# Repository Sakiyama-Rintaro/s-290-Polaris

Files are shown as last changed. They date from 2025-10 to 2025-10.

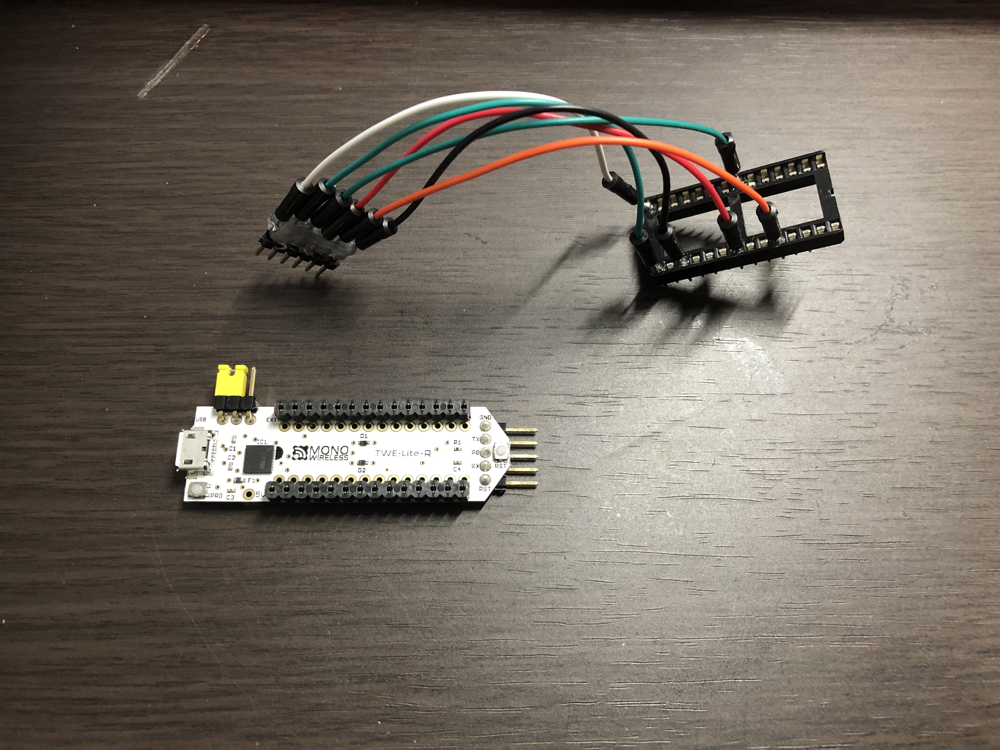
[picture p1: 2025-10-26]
doc/sozai/twelite_programmer.jpg

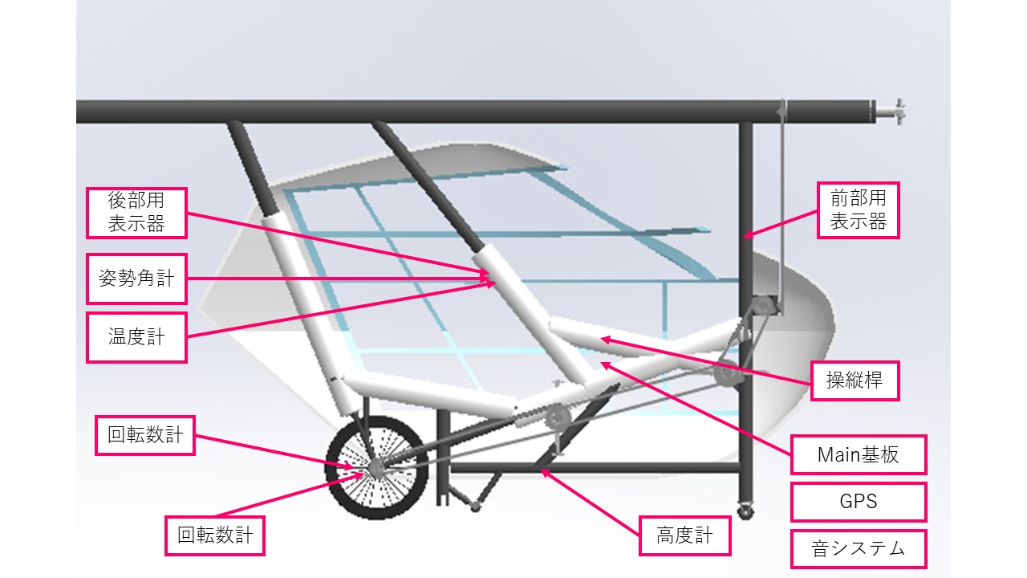
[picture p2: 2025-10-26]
doc/sozai/S-270_Malus_Setsugo_2.jpg

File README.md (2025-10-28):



# S-290 Polaris 電装システム

## はじめに
初めまして。芝浦工業大学理工学研究科電気電子情報学専攻M1の先山倫太郎です。学部時代の学科は工学部電子工学科です。私は学部時代に鳥人間部に所属していて人力飛行機の製作を行っていました。そこでは電装班と呼ばれる機体のシステム系の開発を行なっている班に所属していて、機体の操舵システムと、高度計などの計測器のシステム開発を行っていました。その詳細についてここでは述べさせていただきます。元々プログラミングに興味があり、何かヒントが得られるのではと思い電装班に入った次第です。<br>
<br>
<br>
このリポジトリでは、**人力飛行機電装システム**において<br>
・Mainプリント基板設計・製作<br>
・計測システム・ソフトウェア設計・製作<br>
・操舵システム・ソフトウェア設計・製作<br>
・各種試験系(回転試験・ER試験・全体接合・TF)<br>
に関することが詰まっています。<br>
<br>

なお、フライトデータ表示用のアプリ開発については次のリポジトリを参考にしてください。Androidアプリ開発、Webアプリ開発やその運用方法について記述してあります。<br>
https://github.com/Sakiyama-Rintaro/FlightDisplay.S290<br>

## 後輩の皆さんへ
我々23代電装班では、「同期や後輩の為にしっかりと技術資料を残す」という方針で活動していました。それは、教え合いの文化を形成し効率的な技術力アップを図るためであったり、悲願の鳥コン出場を達成した代なのでこの文化はぜひ引き継いでいったほしいなと思っています。僕からの願いです。<br>
モノづくりを楽しんで、充実した大学生活を送ってください！！<br>

## リポジトリの説明
**・[TBT_S-290_Polaris_System](https://github.com/Sakiyama-Rintaro/s-290-Polaris/tree/main/Module)** //完成品が入っています。プログラム書き込み方法と基板の取り扱いについては、このリポジトリのREADMEを参考にしてください。<br>
**・[Module](https://github.com/Sakiyama-Rintaro/s-290-Polaris/tree/main/Module)** //単体テストで用いたものが入っています。<br>
**・[Yosan](https://github.com/Sakiyama-Rintaro/s-290-Polaris/tree/main/Yosan)** //S-290での購入品についてのデータが入っています。<br>
**・[doc](https://github.com/Sakiyama-Rintaro/s-290-Polaris/tree/main/doc)** //作ったシステムの写真や動画などが入っています。<br>

## 目次
・はじめに<br>
・ソフトウェア・ハードウェア設計ガイド<br>

## 使ったソフト
・GitHub Desktop (GitHub操作用)<br>
・Visual Studio Code (テキストエディタ mbedのコードを書くときに使います)<br>
・LPCISP.exe (lpc1114にプログラムを書きこむときに使います。後で詳細を説明します)<br>
・Tera Term (ターミナル。シリアル通信のデバッグ、Twelite_シリアル通信アプリのモード変更、ER試験等の時に使います<br>
・Realterm (ターミナル。2進数や16進数のデータの確認に使います。Twelite_シリアル通信アプリ_バイナリモード)<br>
・Google Earth Pro (GPSデータのチェックに使います)<br>
・Android Studio (Androidアプリ開発に使います)<br>
・Autodesk Fusion360 (3DCAD。機速計をはじめとする筐体設計に使用します)<br>
・Autodesk Inventor (3DCAD。機速計をはじめとする筐体設計に使用します)<br>
・AutoCAD Mechanical (2DCAD。3DCADだと寸法が確認しづらいので、確認用にこっちも使います。検図チェックお願いします( ﾟДﾟ))<br>
・EAGLE (回路設計CAD。Main基板の設計に使用します。後で詳細を説明します)<br>

## 使用言語
・C/C++ (mbedで使った)<br>
・Kotlin (Androidアプリ開発で使った)<br>

## 使用マイコン(※主要部のみ)
・mbed LPC1768<br>
・mbed LPC1114<br>

# システム全体図
S-290 Malus電装システムの全体図を示します。<br>
各矢印については、<br>
・黒色: シリアル通信(有線) <br>
・緑色: デジタル通信(有線) <br>
・黄色: Zigbee通信(有線) <br>
・赤色: Bluetooth通信(無線) <br>
・青色: モバイルデータ通信(無線) <br>
となっています。<br>
矢印の方向にデータが飛んでいます。<br>
### システム全体図_その1
S-270_Malus_Sysyem_1

### システム全体図_その2
S-270_Malus_System_2

## 各計器・部品等の役割
|計器・部品名|役割|
|---|---|
|[機速計](https://github.com/Sakiyama-Rintaro/s-290-Polaris/blob/main/Module/Airspeed_meter/README.md)|機体の速度(空気に対する相対速度)を計測する|
|[回転数計](https://github.com/Sakiyama-Rintaro/s-290-Polaris/blob/main/doc/picture/Cadence_meter.md)|パイロット達がペダルを回す速さを計測する|
|[高度計](https://github.com/Sakiyama-Rintaro/s-290-Polaris/blob/main/doc/picture/Altimeter.md)|機体の高度を計測する|
|姿勢角計|機体の姿勢情報を計測する|
|心拍計|フライト時におけるパイロット達の心拍数を計測する|
|温度計|サーボモータ付近の温度を計測する|
|[GPS](https://github.com/Sakiyama-Rintaro/s-290-Polaris/blob/main/doc/picture/GPS.md)|機体の現在位置を計測する|
|SD|機速・回転数・高度・姿勢・心拍数・温度・GPS・舵角等の情報を記録する|
|音システム|機体の高度情報を音で知らせる|
|[舵角計](https://github.com/Sakiyama-Rintaro/s-290-Polaris?tab=readme-ov-file)|ER(サーボモータ)の制御角度を表示する|
|[Android端末](https://github.com/Sakiyama-Rintaro/s-290-Polaris/blob/main/doc/picture/Android.md)|前部パイロットにフライト情報を表示する|
|[OLED](https://github.com/Sakiyama-Rintaro/s-290-Polaris0/blob/main/doc/picture/OLED.md)|後部パイロットにフライト情報を表示する|
|Li-Poバッテリー電圧監視システム|サーボモータ用Li-Poバッテリーの残り電圧の情報を記録する|

## システムの設計方針
S-290のシステムでは、無線モジュールtweliteを多用し計測系統の多機能化とパイロット安全の充実化を目指しました。<br>

## S-250からの変更点
・姿勢角計の導入<br>
・心拍計(前部P・後部P)の導入<br>
・温度計の導入<br>
・Li-poバッテリー電源監視システムの導入<br>
・フライト監視システムの導入<br>
・自作出力計の廃止と市販出力計Germin Vector3の導入<br>
・Mainプリント基板の実装部品の変更<br>
・操舵方式の変更<br>
となっています。

## 本システムの良かった点
・無線モジュールを使って、計測システムの多機能化が出来た点<br>
・無線モジュールを使って、接合時間の短縮を目指せた点<br>
・Li-Poバッテリー電圧監視システムにより、パイロット安全が向上した点(現在製作中)<br>

## 本システムの悪かった点
・無線モジュールを沢山使用したことにより、コストが大きくなってしまった点<br>
・表面実装部品の採用により、ハードウェア製作難易度が高い点<br>

# システムの詳細
## 通信方式
本システムで採用しているマイコンのlpc1768とlpc1114では、シリアル通信方式として、UART(通信)、SPI(通信)、I2C(通信)があります。<br>
S-290電装システムにおいて、すべてのシリアル通信によるデータ通信は、UART(通信)のみを使用しました(姿勢角計を除く)。<br>
<br>
<各種計器の設計・製作の観点での理由><br>
コストや製作期間の都合上、各種計器はユニバーサル基板を使って作るのですが、このユニバーサル基板はプリント基板よりもノイズが発生しやすいです。故に、同期式通信でノイズに弱いSPIとI2Cよりもリカバリーが効きやすいUARTを採用しました。<br>
<br>
<Mainプリント基板の設計・製作の観点での理由><br>
配線数が増えて面倒だと思ったため。<br>

## 有線と無線の使い分け
S-290は、有線と無線を組み合わせたシステムとなっています。<br>
人力飛行機の電装システムにおける有線と無線のメリット・デメリットをそれぞれ挙げた後、各計器・部品での採用方式について説明します。<br>
<br>
<有線 メリット><br>
・安定した通信ができる<br>
<有線 デメリット><br>
・配線が必要なため、TFや全体接合等の試験系における接合時間が長くなってしまう<br>
<br>
<無線 メリット><br>
・接合時間を短縮できる<br>
<無線 デメリット><br>
・障害物などの影響で安定しないことがある<br>
・コストが上がる<br>
<br>
|計器・部品名|有線 or 無線|採用理由|
|---|---|---|
|[機速計](https://github.com/Ryosuke-123/doritos.tbt.denso.21st/blob/main/doc/picture/Airspeed_meter.md)|無線|接合時間短縮のため|
|[回転数計](https://github.com/Ryosuke-123/doritos.tbt.denso.21st/blob/main/doc/picture/Cadence_meter.md)|無線|接合時間短縮のため|
|[高度計](https://github.com/Ryosuke-123/doritos.tbt.denso.21st/blob/main/doc/picture/Altimeter.md)|有線|コスト削減のため|
|姿勢角計|無線|接合時間短縮のため|
|心拍計|無線|接合時間短縮のため|
|温度計|無線|接合時間短縮のため|
|[舵角計](https://github.com/Ryosuke-123/doritos.tbt.denso.21st/blob/main/doc/picture/Rudder_Angle_meter.md)|有線|通信の信頼性を上げるため|
|[GPS](https://github.com/Ryosuke-123/doritos.tbt.denso.21st/blob/main/doc/picture/GPS.md)|有線|コスト削減のため|
|SD|有線|プリント基板上に乗せられるほどの余裕があったため|
|スピーカー(音システム)|有線||
|[Android端末](https://github.com/Ryosuke-123/doritos.tbt.denso.21st/blob/main/doc/picture/Android.md)|有線|通信の信頼性を上げるため|
|[OLED](https://github.com/Ryosuke-123/doritos.tbt.denso.21st/blob/main/doc/picture/OLED.md)|有線|通信の信頼性を上げるため|
|サーボモータ|有線|通信の信頼性を上げるため|
|ジョイスティック(操縦桿)|有線|通信の信頼性を上げるため|
|Li-Poバッテリー電圧監視システム|無線|接合時間短縮のため|

## 操舵系統に不具合を起こさない設計
パイロットの命が関わる操舵系統で、トラブルが起こらないように設計しました。<br>
具体的には、操舵用マイコンには他のマイコンからデータを送り付けないようにし、データ処理が追い付かず操舵に影響が出ないようにしました。

## パイロット達が安全措置を行える設計
Android端末、OLED、音システム、舵角計、リポバッテリー電圧監視システムを採用し、パイロットや併走艇に乗る全体設計者が機体の状況を常に把握できるようにしました。

## 前部P用表示器と後部P用表示器に映す情報の使い分け
TBTの機体は、他チームの機体と異なり2人乗りです。つまりパイロットが2人居るということです。<br>
実際の航空機において機長と副操縦士が操縦とフライト情報のモニタリングを分けて行うように、TBTのパイロット達にも役割分担をさせましょう。1人で処理できる情報には限りがありますからね( ﾟДﾟ)。<br>
S-290では、以下のようにしました。<br>
<br>
<前部パイロット><br>
操縦優先。舵角計や高度情報などフライト操縦に必要な情報のみを表示。進路方向や風向きの状況判断など、意思決定権を持つ。<br>
視界が見えやすく、操縦悍を持っているため基本的には漕ぎながら操縦に集中してもらう。<br>
<br>
<後部パイロット><br>
表示確認→全部パイロットへ伝達を担当。また後部のみアップライト型なのでとにかく出力を出して前部パイロットを支援する。<br>
全体的に前部パイロットの補佐の役割を担う。<br>
<br>
# 設計に関する勉強について

## 電装設計&責任者の年間スケジュールについて
S-290では、コロナによる学内活動禁止が繰り返し行われたため、製作スケジュールに大きな影響をもたらしました。(別の要因もありましたが...)<br>
以下に、僕の当初の活動予定と実際の活動状況について示した表を示します。今後の参考にしてください。<br>

|月|予定|記録|
|---|---|---|
|8月|ひたすら勉強、TP(テストピース)作成、運営陣会議|新入生集め|
|9月|P選考、勉強、TP作成|勉強、TP作成、新入生集め、活動方針決定、運営陣会議|
|10月|勉強、TP作成|勉強、TP作成、P選考|
|11月|勉強、TP作成|勉強、TP作成|
|12月|マザボプロトタイプ製作、プリント基板発注|勉強、TP作成|
|1月|Main基板部品実装・ソフトウェア作成、鳥コン書類執筆|勉強、TP作成|
|2月|マザボほぼ完成、CF三昧、利根川精工にサーボ発注|マザボプロトタイプ製作、プリント基板発注|
|3月|マザボ調整・各種計器作成|プリント基板再発注、CF三昧|
|4月|全体接合・回転試験・ER試験準備、マザボ調整|Main基板部品実装・ソフトウェア作成、CF三昧|
|5月|全体接合・回転試験・ER試験準備、マザボ調整|マザボほぼ作成、各種計器作成|
|6月|TF、マザボ調整|TF,マザボ調整||
|7月|TF、鳥コン|TF、鳥コン||

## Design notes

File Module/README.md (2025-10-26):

# 各フォルダについての説明

|フォルダ|内容|
|:---:|:---:|
|Airspeed_meter|機速計|
|Altimeter|高度計|
|Android|Android表示計(前部パイロット用表示計)|
|ArcGIS|GISソフトウェア|
|Cadence_meter|回転数計|
|ER_lpc1768|エレベータ、ラダー制御プログラム(サーボモータ)|
|Li-Po|リポバッテリー電圧監視システム(7セグメントディスプレイ)|
|Main_lpc1768|メインボードマイコン(各センサ情報統合など)|
|OLED|OLED表示計(後部パイロット用表示計)|
|Printed_circuit_board_design|メイン基板|
|Rudder_angle_meter|舵角計|
|Server|Android周りサーバー関係|
|Sound_lpc1114|警報システム|
|Twe_lpc1114|無線情報統合用(機速、回転数、姿勢角、心拍、温度)|

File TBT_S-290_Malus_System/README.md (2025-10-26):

## はじめに
S-270 Malus電装システムにおけるMain基板のシステムを再現するために必要なことが書かれています。参考にしてください。<br>

## 各ファイルについて
・S-270_Malus_board.zip : Fusion PCBにて発注するデータ<br>
・S-270_Malus_Main_board.sch : メイン基板回路図<br>
・S-270_Malus_Main_board.brd : メイン基板配線図<br>
・S-270_Malus_Main_board_sch.png : メイン基板回路図写真<br>
・S-270_Malus_Main_board_brd.png : メイン基板配線図写真<br>
・S-270_Malus_board_parts : プリント基板に使った部品一覧 <br>
・Android_System_for_test : Androidプログラム。数字表示するだけ<br>
・S-270_main_lpc1768.cpp : 計測用マイコンプログラム<br>
・S-270_ER_lpc1768.cpp : 操舵用マイコンプログラム<br>
・S-270_twe_lpc1114.cpp : 無線モジュール用マイコンプログラム<br>
・S-270_gps_lpc1114.cpp : GPS用マイコンプログラム<br>
・S-270_sound_lpc1114.cpp : 音システム用マイコンプログラム<br>
・S-270_airspeed_meter_lpc1114 : 対気速度計用マイコンプログラム(送信機)<br>
・S-270_cadence_meter_lpc1114 : 回転数計用マイコンプログラム(送信機)<br>

## 目次
・基板準備<br>
・部品実装<br>
・自作書き込み機の準備<br>
・書き込みソフトウェアの準備<br>

## 基板準備
### Step1
リポジトリから「S-270_Malus_board.zipファイル」をダウンロードする。<br>

### Step2
Fusion PCBのサイト[(Click Here)](https://www.fusionpcb.jp/fusion_pcb.html)に行き、ダウンロードしたzipファイルをアップロードする。<br>
  (設定) <br>
  ・材質: FR-4 TG130 <br>
  ・層数: 二層 <br>
  ・寸法: 80.0 * 100.0 <br>
  ・製造枚数: 好きな枚数 <br>
  ・異種面付けの種類: 1 <br>
  ・板厚: 1.60 <br>
  ・レジスト色: 好きな色 <br>
  ・基板の表面処理: HASL(有鉛半田レベラー) <br>
  ・最小ソルダレジストダムの幅: 0.4mm↑ <br>
  ・銅箔厚: 1oz. <br>
  ・最小穴径: 0.3mm <br>
  ・最小パターン幅/パターン間隔: 6/6 mil <br>
  ・端面スルーホール: なし <br>
  ・インピーダンス制御: なし <br>
  
### Step3
ページの指示に従って、発注をかける。<br>

## 部品実装
届いた基板に部品を実装しましょう。<br>
使用する部品は、「S-270_Malus_board_parts.xlsx」に記載されています。<br>

## 自作書き込み機の準備
### lpc1114FDH28(表面実装版lpc1114)用書き込み機
S-270で使った書き込み機の写真とその回路配線についての写真を下に示します。<br>
<写真><br>
lpc1114_programmer
<回路図><br>
lpc1114_programmer

### 表面実装版twelite用書き込み機
S-270で使った書き込み機の写真とその回路配線についての写真を下に示します。<br>
<写真><br>
twelite_programmer
<回路図><br>
twelite_programmer

## 書き込み用ソフトウェアの準備
lpc1114FDH28とtweliteへのプログラム書き込みには、それぞれ専用のソフトウェアが必要です。<br>
まずは、必要なソフトウェアをダウンロードしましょう。<br>
<br>
・LPCISP.exe(lpc1114FDH28への書き込みに必要) [Click!](https://synapse.kyoto/tips/LPC1114/page002.html)<br>
・TWE-Programmer.exe(tweliteへの書き込みに必要) [Click!](https://mono-wireless.com/jp/products/TWE-APPS/LiteProg/index.html)<br>
・Tera Term(tweliteに書き込む「シリアル通信アプリ」のターミナル設定に必要) [Click!](https://forest.watch.impress.co.jp/library/software/utf8teraterm/)<br>
<br>

### lpc1114FDH28への書き込み

### tweliteへの書き込みと設定

・Device ID: 0x00<br>
・UART band: 115200<br>
・UART mode: Binary formatted<br>

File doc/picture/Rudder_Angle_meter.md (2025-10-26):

Rudder_Angle_Meter

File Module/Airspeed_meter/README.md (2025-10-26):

# 機速計(対気速度計)について

### 機速計とは
機速計とは、航空機の速度を示す機器です。航空機は、乗用車やバイクと異なり地面から離れ大気中を航行します。その為、ここでいう航空機の速度とは大気との相対速度を示していることを理解してください。

### 原理
機速計には、様々な種類があります。今回は、鳥人間界隈において多くのチームが採用しているプロペラ式機速計の原理について説明します。<br>
下の図に示してあるのが、プロペラ式機速計です。まずはどんな部品が使われているのかリバースエンジニアリングしてみましょう。<br>
プロペラ式機速計

プロペラ式機速計をリバースエンジニアリングしてみると、<br>
・プロペラ<br>
・ベアリング<br>
・中空シャフト<br>
・スリット円盤<br>
・フォトインタラプタ<br>
・lpc1114<br>
・twelite<br>
・電池<br>
の8部品で構成されていることが分かります。<br>

プロペラ式機速計において、最も重要な要素・部品はフォトインタラプタであると言えます。<br>
それでは続いて、フォトインタラプタについて探っていきましょう。<br>

### 校正方法

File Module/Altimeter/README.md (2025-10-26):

### 高度計について <br>
　高度計とは、機体が水面(地面)からどれくらいの高さで飛んでいるかを計測する機器である。<br>

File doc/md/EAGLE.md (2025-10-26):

## EAGLE(電子回路設計用CAD)の使い方

## EAGLEとは？
EAGLEとは、電子回路の基板パターンを設計する電子回路CADソフトです。
回路基板上の導体パターンの設計や基板外観形状、シルクパターン、接点の配置などを決めて、実際の電子回路に落とし込むために使われます。<br>

## EAGLEのインストール
EAGLEには、<br>
1. EAGLE Free <br>
2. EAGLE Premium <br> の2つのバージョンがあります。<br>
料金が無料であるEAGLE Freeをダウンロードしましょう。<br>

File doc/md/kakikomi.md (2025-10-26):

## 表面実装版 lpc1114 & twelite のプログラム書き込み方法についてのガイド

### lpc1114への書き込み方法

### tweliteへの書き込み方法

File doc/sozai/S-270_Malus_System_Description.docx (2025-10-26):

S-270 Malus電装システムについて

S-270 Malus電装設計&責任者: 檜山凌祐(Doritos)

1. システムの概要

S-270 Malus電装システムの全体図を図1, 2に示す.

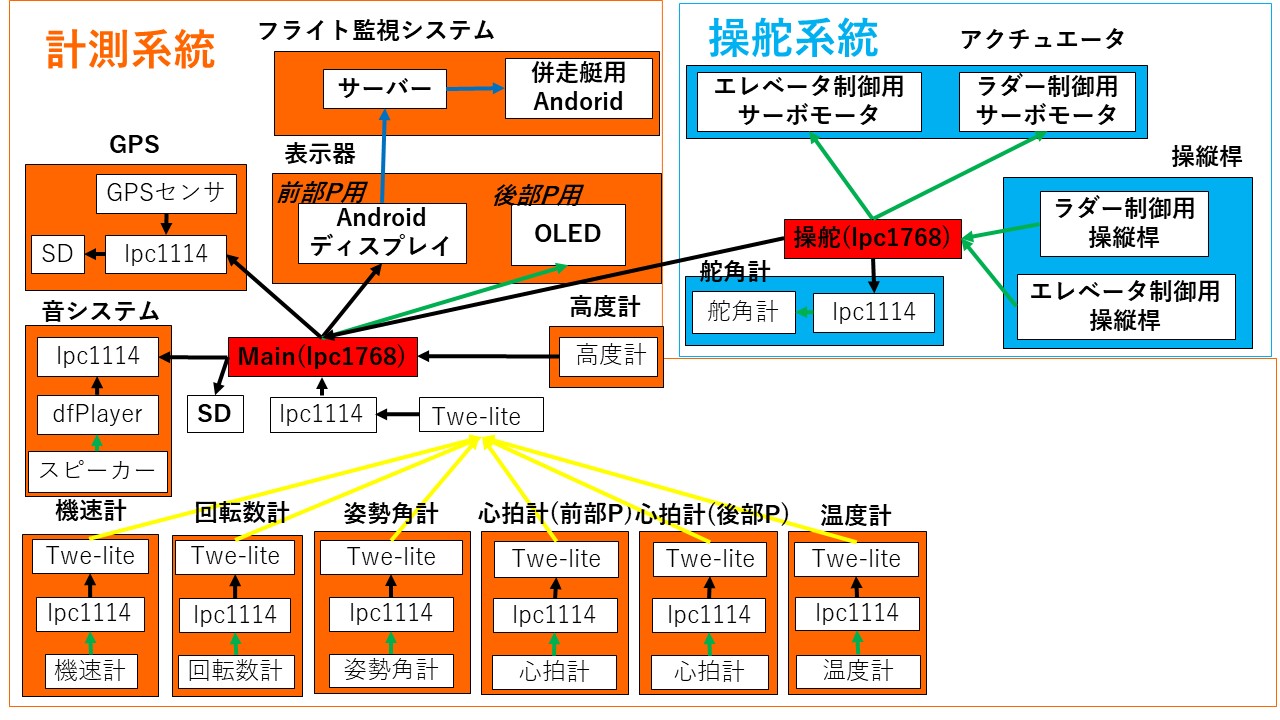
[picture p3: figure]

図1. S-270 Malus電装システム_全体図_その1

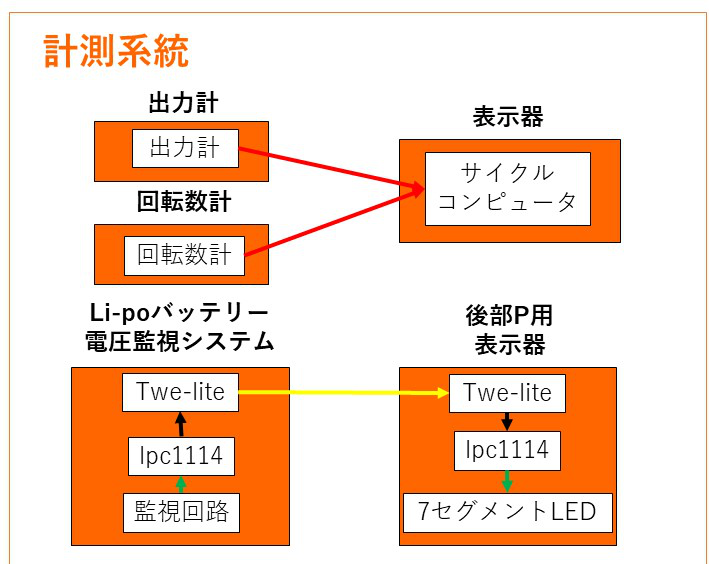
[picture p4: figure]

図2. S-270 Malus電装システム_全体図_その2

<各矢印について>

・黒色: シリアル通信(有線)

・緑色: デジタル通信(有線)

・黄色: Zigbee通信(無線)

・赤色: Bluetooth通信(無線)

・青色: モバイルデータ通信(無線)

  1-1. システムの設計方針

S-270のシステムでは, S-250のシステムをベースとし, 計測系統の多機能化とパイロット安全の充実化を目指した.

  1-2. S-250からの変更点

・姿勢角計の導入

・心拍計(前部P・後部P)の導入

・温度計の導入

・Li-poバッテリー電圧監視システムの導入

・フライト監視システムの導入

・自作出力計の廃止と市販出力計Germin Vector3の導入

  1-3. 本システムの良かった点
  1-4. 本システムの悪かった点

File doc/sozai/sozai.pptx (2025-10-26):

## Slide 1

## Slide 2

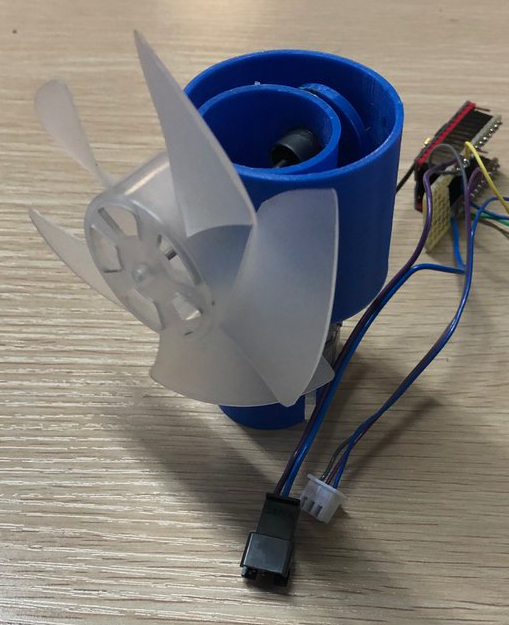
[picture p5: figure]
芝浦鳥人間2020新歓@入部受付中 on Twitter: "電装班 紹介1 〜機速計 ...

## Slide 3

Andorid端末

ER操作用サーボモータ

OLED

操縦桿
(2軸ジョイスティック)

lpc11u35fhi33/501

Main(lpc1768fdb100)

ER(lpc1768fdb100)

高度計

lpc11u35fhi33/501

GPS

lpc1114

機速計

機速計

lpc1114

Twe-lite

回転数計

回転数計

lpc1114

Twe-lite

SD

SD

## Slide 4

計測系統

フライト監視システム

併走艇用Andorid

操舵系統

アクチュエータ

ラダー制御用
サーボモータ

サーバー

エレベータ制御用
サーボモータ

GPSセンサ

lpc1114

GPS

前部P用

表示器

後部P用

OLED

ラダー制御用
操縦桿

エレベータ制御用
操縦桿

操縦桿

SD

Android
ディスプレイ

操舵(lpc1768)

音システム

lpc1114

dfPlayer

スピーカー

機速計

高度計

高度計

舵角計

舵角計

lpc1114

SD

Main(lpc1768)

lpc1114

Twe-lite

姿勢角計

心拍計(前部P)

Twe-lite

lpc1114

機速計

回転数計

Twe-lite

lpc1114

回転数計

Twe-lite

lpc1114

姿勢角計

Twe-lite

lpc1114

心拍計

心拍計(後部P)

Twe-lite

lpc1114

心拍計

温度計

Twe-lite

lpc1114

温度計

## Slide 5

計測系統

出力計

出力計

回転数計

表示器

サイクル
コンピュータ

回転数計

Li-poバッテリー
電圧監視システム

Twe-lite

監視回路

後部P用
表示器

Twe-lite

7セグメントLED

lpc1114

lpc1114

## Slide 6

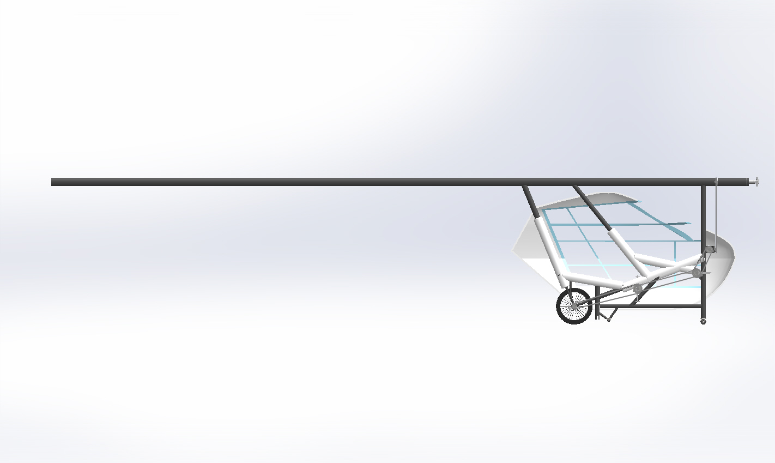
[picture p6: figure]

Li-poバッテリー
電圧監視システム

機速計

サーボモータ

有線通信

キングポスト

サーボモータ

Li-po
バッテリー

無線通信

Main基板

後部用
表示器

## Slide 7

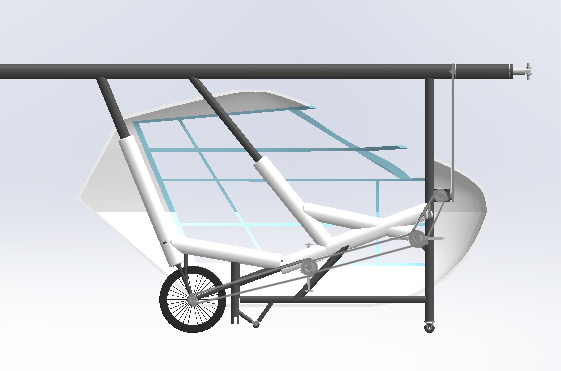
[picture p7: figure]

後部用
表示器

前部用
表示器

姿勢角計

温度計

操縦桿

回転数計

Main基板

回転数計

高度計

GPS

音システム

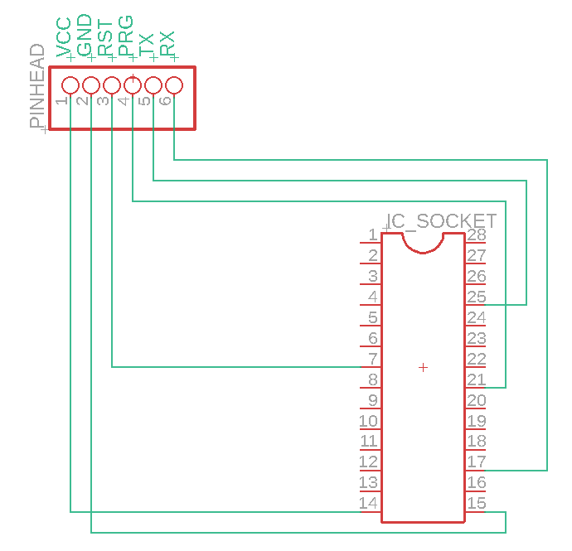
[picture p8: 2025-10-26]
doc/sozai/twelite_programmer_sch.png

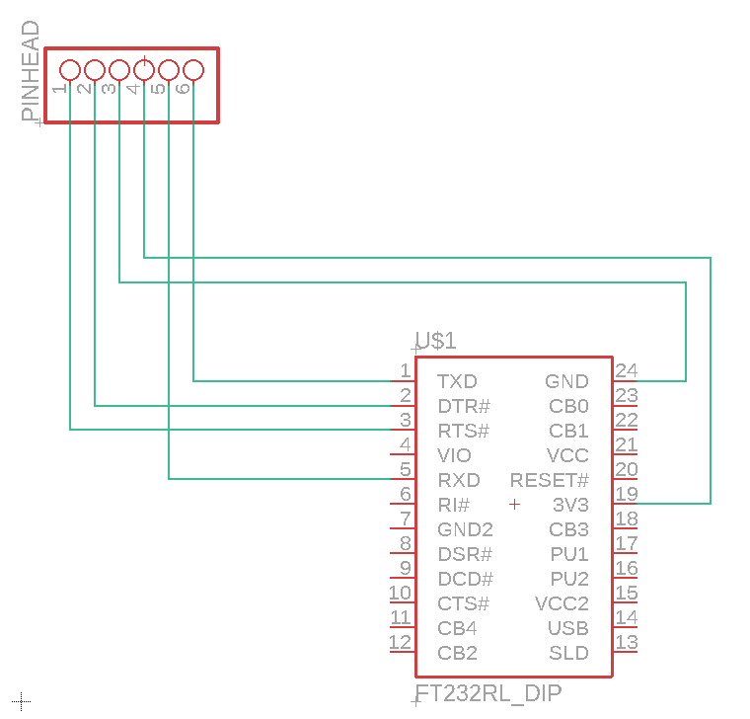
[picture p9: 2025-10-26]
doc/sozai/lpc1114_programmer_sch.jpg

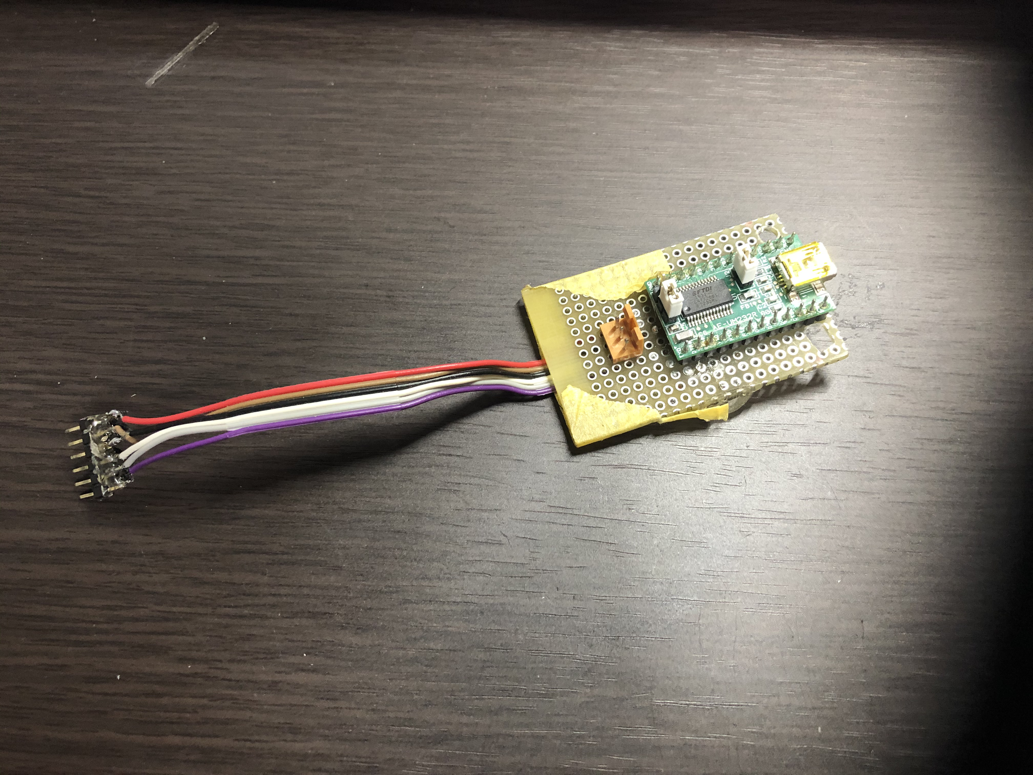
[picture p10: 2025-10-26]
doc/sozai/lpc1114_programmer.jpg

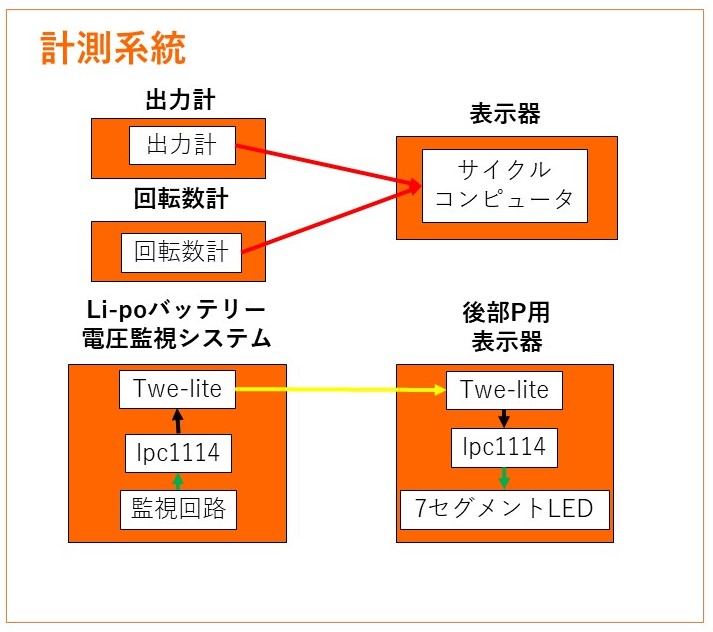
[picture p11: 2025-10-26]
doc/sozai/S-270_Malus_System_2.jpg

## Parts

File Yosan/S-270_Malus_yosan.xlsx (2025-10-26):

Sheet: 購入品
商品名 | 金額 | 個数 | 小計 | 合計
LPCマイコン LPC1768FBD | 1140 | 4 | 4560 | 45181
LPCマイコン LPC11U35 | 350 | 2 | 700
LPCマイコン LPC1114FDH28 | 300 | 11 | 3300
LPCマイコン LPC1114FDH28 | 200 | 3 | 600
トワイライトワイヤレスモジュール TWE-Lite アンテナ | 1450 | 5 | 7250
トワイライト平面アンテナ | 550 | 1 | 550
FTDI USBシリアル変換ケーブル(3.3V) | 1950 | 1 | 1950
USBシリアル変換IC FT232RL | 400 | 3 | 1200
スーパー三端子レギュレータ 3.3V500mA | 350 | 5 | 1750
基板取付用スピーカーユニット | 100 | 1 | 100
基板取付用LANコネクタ(モジュラージャック) | 100 | 4 | 400
基板取付用USBコネクタ・ミニB・メス | 200 | 1 | 200
表面実装型クリスタル(水晶発振子) 12MHz | 200 | 2 | 400
表面実装用タクトスイッチ 2.55N | 100 | 2 | 200
リセットIC TCM809R | 200 | 1 | 200
PchMOSFET IRLML2246TRPBF(10個入り) | 200 | 1 | 200
ESD保護デバイス LXES11DAA2-137 | 250 | 1 | 250
低飽和型レギュレーター 3.3V150mA | 150 | 1 | 150
3㎜緑色LED | 200 | 2 | 400
青色チップLED 1608サイズ | 150 | 1 | 150
青色チップLED 1608サイズ | 200 | 1 | 200
KOA チップ抵抗 1608サイズ 10Ω | 50 | 4 | 200
KOA チップ抵抗 1608サイズ 22Ω | 50 | 1 | 50
KOA チップ抵抗 1608サイズ 200Ω | 50 | 2 | 100
KOA チップ抵抗 1608サイズ 1kΩ | 50 | 2 | 100
KOA チップ抵抗 1608サイズ 1.5kΩ | 50 | 1 | 50
KOA チップ抵抗 1608サイズ 2.2kΩ | 50 | 1 | 50
チップ積層セラミックコンデンサー 0.01µF50V | 100 | 1 | 100
チップ積層セラミックコンデンサー 0.1µF50V | 100 | 1 | 100
チップ積層セラミックコンデンサー 4.7µF10V | 100 | 1 | 100
チップ積層セラミックコンデンサー 10µF35V | 150 | 1 | 150
基板用小型3Pトグルスイッチ 1回路2接点 | 80 | 9 | 720
基板用小型3Pトグルスイッチ 1回路2接点 | 90 | 10 | 900
ヒロセ・マイクロSDカードコネクタ | 140 | 2 | 280
XHコネクタ ベース付ポスト サイド型2P | 10 | 10 | 100
XHコネクタ ベース付ポスト サイド型3P | 10 | 10 | 100
XHコネクタ ハウジング用コンタクト | 200 | 1 | 200
ジャンパーピン白(2.54mmピッチ) | 100 | 1 | 100
分割ロングピンソケット 1×42(42P) | 80 | 1 | 80
ピンヘッダ 1×40(40P) | 35 | 1 | 35
高密度集積基板ハンダ0.6mm | 280 | 2 | 560
au Xperia XZ SOV34 Platinum 中古Cランク | 6980 | 1 | 6980
プリント基板発注代(1回目) 2021年1月13日 | 2132 | 1 | 2132
プリント基板発注代(2回目) 2021年2月20日 | 2099 | 1 | 2099
プリント基板発注代(3回目) 2021年2月21日 | 2525 | 1 | 2525
プリント基板発注代(4回目) 2021年2月25日 | 2652 | 1 | 2652
レジ袋 | 3 | 1 | 3
ビニール手提げ袋(小) | 5 | 1 | 5

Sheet: 予定
購入予定物 | 個数 | 値段(1個) | 小計 | 合計
LPC1768 | 5 | 7000 | 35000 | 203624
LPC1114FN28 | 4 | 400 | 1600
利根川サーボPS-050 | 2 | 30000 | 60000
GPS受信機キット 1PPS出力付き 「みちびき」３機受信対応 | 3 | 2100 | 6300
トワイライト平面アンテナ TWE-AN-P4208-100 | 2 | 550 | 1100
トワイライトワイヤレスモジュール TWE-Lite アンテナ別付けタイプ | 1 | 1450 | 1450
トワイライトワイヤレスモジュール TWE-Lite-RED アンテナ別付けタイプ | 1 | 2470 | 2470
トワイライトワイヤレスモジュール TWE-Lite-Red-Dip ワイヤアンテナ | 2 | 3030 | 6060
トワイライトワイヤレスモジュール TWE-Lite-Dip-WA （完成品） | 2 | 1980 | 3960
透過型フォトインタラプタ SG206 | 10 | 100 | 1000
超音波センサMB1360 | 3 | 6560 | 19680
Li-Poバッテリー Hyperion G5 SV 35-70C 放電 2200mAh 3S(11.1V)金 | 2 | 2960 | 5920
片面ガラス・ユニバーサル基板Ａタイプ2.54㎜ピッチ（155×114㎜） | 2 | 350 | 700
両面スルホール・ガラス・ユニバーサル基板Ａタイプ2.54㎜ピッチ（155×114㎜） | 2 | 400 | 800
片面ガラスコンポジット・ユニバーサル基板 Ｃタイプ めっき仕上げ （72×47㎜） 日本製 | 2 | 60 | 120
両面スルーホールガラスコンポジット・ユニバーサル基板 Ｃタイプ めっき仕上げ 72×47㎜ 日本製 | 2 | 90 | 180
3㎜プラネジ（7㎜）＋六角スペーサー（14㎜）セット | 4 | 50 | 200
超高輝度5mm赤色LED OS5RKA5111P(10個入) | 1 | 250 | 250
超高輝度5mm青色LED OSB56A5111A(10個入) | 1 | 220 | 220
超高輝度5mm緑色LED OSG58A5111A(10個入) | 1 | 200 | 200
LED光拡散キャップ(5mm) 白 (50個入) | 1 | 200 | 200
高輝度3㎜赤色LED OSR7CA3131A（１０個入） | 1 | 200 | 200
超高輝度３ｍｍ緑色ＬＥＤ ＯＳＧ５８Ａ３１３１Ａ（１０個入） | 1 | 200 | 200
ＬＥＤ光拡散キャップ（３ｍｍ） 白 （２０個入） | 1 | 100 | 100
基板用小型3Pトグルスイッチ 1回路2接点 | 5 | 80 | 400
超効率DC-DCコンバーター 3.3V1A M78AR33-1 | 1 | 500 | 500
分割ロングピンソケット １×４２ （４２Ｐ | 3 | 80 | 240
ＸＨコネクタ ハウジング用コンタクト SXH-001T-P0.6 (100個入り) | 1 | 200 | 200
ＸＨコネクタ ハウジング ２Ｐ ＸＨＰ－２ | 20 | 5 | 100
ＸＨコネクタ ベース付ポスト サイド型 2P S2B-XH-A(LF)（SN） | 20 | 10 | 200
ＸＨコネクタ ベース付ポスト トップ型 ２P B2B-XH-A(LF)（SN） | 20 | 10 | 200
ＸＨコネクタ ハウジング 3P XHP-3 | 20 | 5 | 100
ＸＨコネクタ ベース付ポスト サイド型 3P S3B-XH-A(LF)（SN） | 20 | 10 | 200
ＸＨコネクタ ベース付ポスト トップ型 3P B3B-XH-A(LF)（SN） | 20 | 10 | 200
LANコネクタDIP化キット | 3 | 200 | 600
OLED | 2 | 2638 | 5276
２種ポリウレタン銅線 2UEW 0.29㎜ 100g | 1 | 900 | 900
基板取付用スピーカーユニット UGSM30B-8-01 | 2 | 100 | 200
dfプレーヤーmini | 3 | 1050 | 3150
LSM9DS1 9軸慣性計測ユニット ピッチ変換済みモジュール | 3 | 1650 | 4950
FT232RL USBシリアル変換モジュール | 1 | 950 | 950
【SIMロック解除済】 au Xperia XZs SOV35 Warm Silver | 1 | 11800 | 11800
Eagle プリント基板発注代 |  |  | 3600
LPC1114FN28 | 1 | 2200 | 2200
ブレッドボード・ジャンパワイヤ(オス-メス) 10cmセット | 1 | 180 | 180
圧電スピーカ(圧電サウンダ)SPT08(2個入) | 1 | 100 | 100
CdSセル(0.5MΩ)GL5516(4個入) | 1 | 100 | 100
3mm赤色LED 70° OSR5JA3Z74A | 2 | 10 | 20
単一乾電池 4本 | 1 | 449 | 449
単三乾電池 4本 | 1 | 349 | 349
マイクロサーボ SG92R | 2 | 500 | 1000
カーボン抵抗(炭素皮膜抵抗) 1/4W1kΩ(100本入) | 1 | 100 | 100
ブレッドボード EIC-801 | 1 | 270 | 270
高輝度３ｍｍ白色LED LEBWL34A06AA00 | 2 | 10 | 20
外装雑費費 | 1 | 1000 | 1000
基板用小型3Pトグルスイッチ 1回路2接点 | 3 | 80 | 240
片面ガラス・ユニバーサル基板 Cタイプ(72×47.5mm) | 1 | 60 | 60
丸ピンICソケット(16P) | 1 | 30 | 30
電池ボックス 単3×2本 リード線・間仕切りあり | 1 | 50 | 50
Grove ジョイスティックモジュール | 1 | 780 | 780
予備費 |  |  | 15000

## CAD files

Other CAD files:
Module/Airspeed_meter/hardware/Slit_disk.dwg
Module/Airspeed_meter/hardware/Slit_disk.ipt

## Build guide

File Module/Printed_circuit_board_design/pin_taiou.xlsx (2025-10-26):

計測用(Main)_lpc1768 |  |  |  | 操舵用(ER)_lpc1768
接続先 | ピン | ピン | 接続先 | 接続先 | ピン | ピン | 接続先
GNDライン | GND | VOUT |  | GNDライン | GND | VOUT
MAIN・ER用マイコン&GPSモジュール電源投入用スイッチ | VIN | VU |  | MAIN・ER用マイコン&GPSモジュール電源投入用スイッチ | VIN | VU
 | VB | IF- |  |  | VB | IF-
 | nR | IF+ |  |  | nR | IF+
 | p5 | RD- |  |  | p5 | RD-
 | p6 | RD+ |  |  | p6 | RD+
 | p7 | TD- |  |  | p7 | TD-
 | p8 | TD+ |  |  | p8 | TD+
to SD(OpenLog) | p9 | D- |  | to 計測用_lpc1768 | p9 | D-
from gps_lpc1114 | p10 | D+ |  |  | p10 | D+
to OLED用LANコネクタ | p11 | p30 | to OLED用LANコネクタ |  | p11 | p30
to OLED用LANコネクタ | p12 | p29 | to OLED用LANコネクタ |  | p12 | p29
to USB Serial変換モジュール(Android) | p13 | p28 | to sound_lpc1114 | to 舵角計用コネクタ | p13 | p28
from twe_lpc1114 | p14 | p27 | from 操舵用_lpc1768 |  | p14 | p27
to OLED用LANコネクタ | p15 | p26 |  |  | p15 | p26 | From Rudder Trim-Switch(Left)
to OLED用LANコネクタ | p16 | p25 |  |  | p16 | p25 | From Rudder Trim-Switch(Right)
to gps_lpc1114 | p17 | p24 | from 回転数計用コネクタ |  | p17 | p24 | From Eleveter Trim-Switch(UP)
 | p18 | p23 | from 音量切り替えスイッチ(UP)用コネクタ |  | p18 | p23 | From Eleveter Trim-Switch(Down)
 | p19 | p22 | from 音量切り替えスイッチ(DOWN)用コネクタ | from エレベータ制御ジョイスティック用コネクタ | p19 | p22 | to エレベータサーボPWM制御用コネクタ
from 高度計用コネクタ | p20 | p21 | from ログスイッチ用コネクタ | from ラダー制御ジョイスティック用コネクタ | p20 | p21 | to ラダーサーボPWM制御用コネクタ
PC | USBコネクタ |  |  | PC | USBコネクタ
Twe_lpc1114 |  |  |  | GPS_lpc1114
接続先 | ピン | ピン | 接続先 | 接続先 | ピン | ピン | 接続先
 | dp1 | dp28 |  |  | dp1 | dp28
 | dp2 | dp27 |  |  | dp2 | dp27
 | SWCLK | dp26 |  |  | SWCLK | dp26
 | dp4 | dp25 |  | from 計測用_lpc1768 | dp4 | dp25
 | dp5 | dp24 | twe_lpc1114書き込み用穴 |  | dp5 | dp24 | gps_lpc1114書き込み用穴
 | dp6 | nR | twe_lpc1114書き込み用穴 |  | dp6 | nR | gps_lpc1114書き込み用穴
 | AVIN | GND | GNDライン & twe_lpc1114書き込み用穴 |  | AVIN | GND | GNDライン & gps_lpc1114書き込み用穴
 | AGND | VIN | 計測用IC 電源投入用スイッチ & twe_lpc1114書き込み用穴 |  | AGND | VIN | 計測用IC 電源投入用スイッチ & gps_lpc1114用書き込み穴
 | dp9 | Xtalln |  |  | dp9 | Xtalln
 | dp10 | XtalOut |  |  | dp10 | XtalOut
 | dp11 | dp18 |  |  | dp11 | dp18
 | SWDIO | dp17 |  |  | SWDIO | dp17
 | dp13 | dp16 | to 計測用_lpc1768 & twe_lpc1114書き込み用穴 |  | dp13 | dp16 | to OpenLog and 計測用_lpc1768 & gps_lpc1114書き込み用穴
 | dp14 | dp15 | from Twe-lite & twe_lpc1114書き込み用穴 |  | dp14 | dp15 | from GPSモジュール用コネクタ & gps_lpc1114書き込み用穴
Sound_lpc1114 |  |  |  | USBシリアル変換モジュール
接続先 | ピン | ピン | 接続先 | 接続先 | ピン | ピン | 接続先
 | dp1 | dp28 |  |  | TXD+ | GND | GNDライン
 | dp2 | dp27 |  |  | DTR# | CB0
 | SWCLK | dp26 |  |  | RTS# | CB1
 | dp4 | dp25 |  |  | VIO | Vcc
 | dp5 | dp24 | sound_lpc1114書き込み用穴 | from Mainマイコン | RXD | RST
 | dp6 | nR | sound_lpc1114書き込み用穴 |  | RI# | 3V3
 | AVIN | GND | GNDライン & sound_lpc1114書き込み用穴 |  | GND | CB3
 | AGND | VIN | 計測用IC 電源投入用スイッチ & sound_lpc1114書き込み用穴 |  | DSR# | PU1
 | dp9 | Xtalln |  |  | DCD# | PU2
 | dp10 | XtalOut |  |  | CTS# | Vcc
 | dp11 | dp18 |  |  | CB4 | USB
 | SWDIO | dp17 |  |  | CB2 | SLD
 | dp13 | dp16 | to Dfplayer Mini & sound_lpc1114書き込み用穴 | to Android端末 | USBコネクタ
 | dp14 | dp15 | from 計測用_lpc1768 & sound_lpc1114書き込み用穴
Twelite(表面実装版)
接続先 | ピン | ピン | 接続先
 | 1 | 32
Twelite書き込み用穴 | 2 | 31
 | 3 | 30
 | 4 | 29
計測用IC 電源投入用スイッチ & Twelite書き込み用穴 | 5 | 28 | GNDライン & Twelite書き込み用穴
 | 6 | 27
 | 7 | 26
to twe_lpc1114 & Twelite書き込み用穴 | 8 | 25
Twelite書き込み用穴 | 9 | 24
 | 10 | 23
 | 11 | 22
 | 12 | 21 | Twelite書き込み用穴
 | 13 | 20
 | 14 | 19
 | 15 | 18
 | 16 | 17

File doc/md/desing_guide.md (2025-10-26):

## プリント基板設計ガイド

## 基板設計の流れ
基板設計の流れは以下の通りです。</br>
1. 仕様設計 これから構築するシステムの仕様を大まかに決めます。</br>
2. 部品選定 プリント基板に実装する部品を選定します。</br>
3. 部品調達 部品を調達します。</br>
4. プリント基板設計 EAGLEやKiCadといった回路設計CADを用いて、回路図・配線図を作成します。</br>
5. 発注 設計した図面を送ります。</br>
6. 部品実装 届いたプリント基板に部品を実装します。はんだづけです。</br>
7. 評価 設計・開発した基板の評価・検証を実施し、不具合が無いか確認します。</br>

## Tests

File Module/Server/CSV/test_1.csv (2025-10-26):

Name | Score
Mike | 90
Bob | 95

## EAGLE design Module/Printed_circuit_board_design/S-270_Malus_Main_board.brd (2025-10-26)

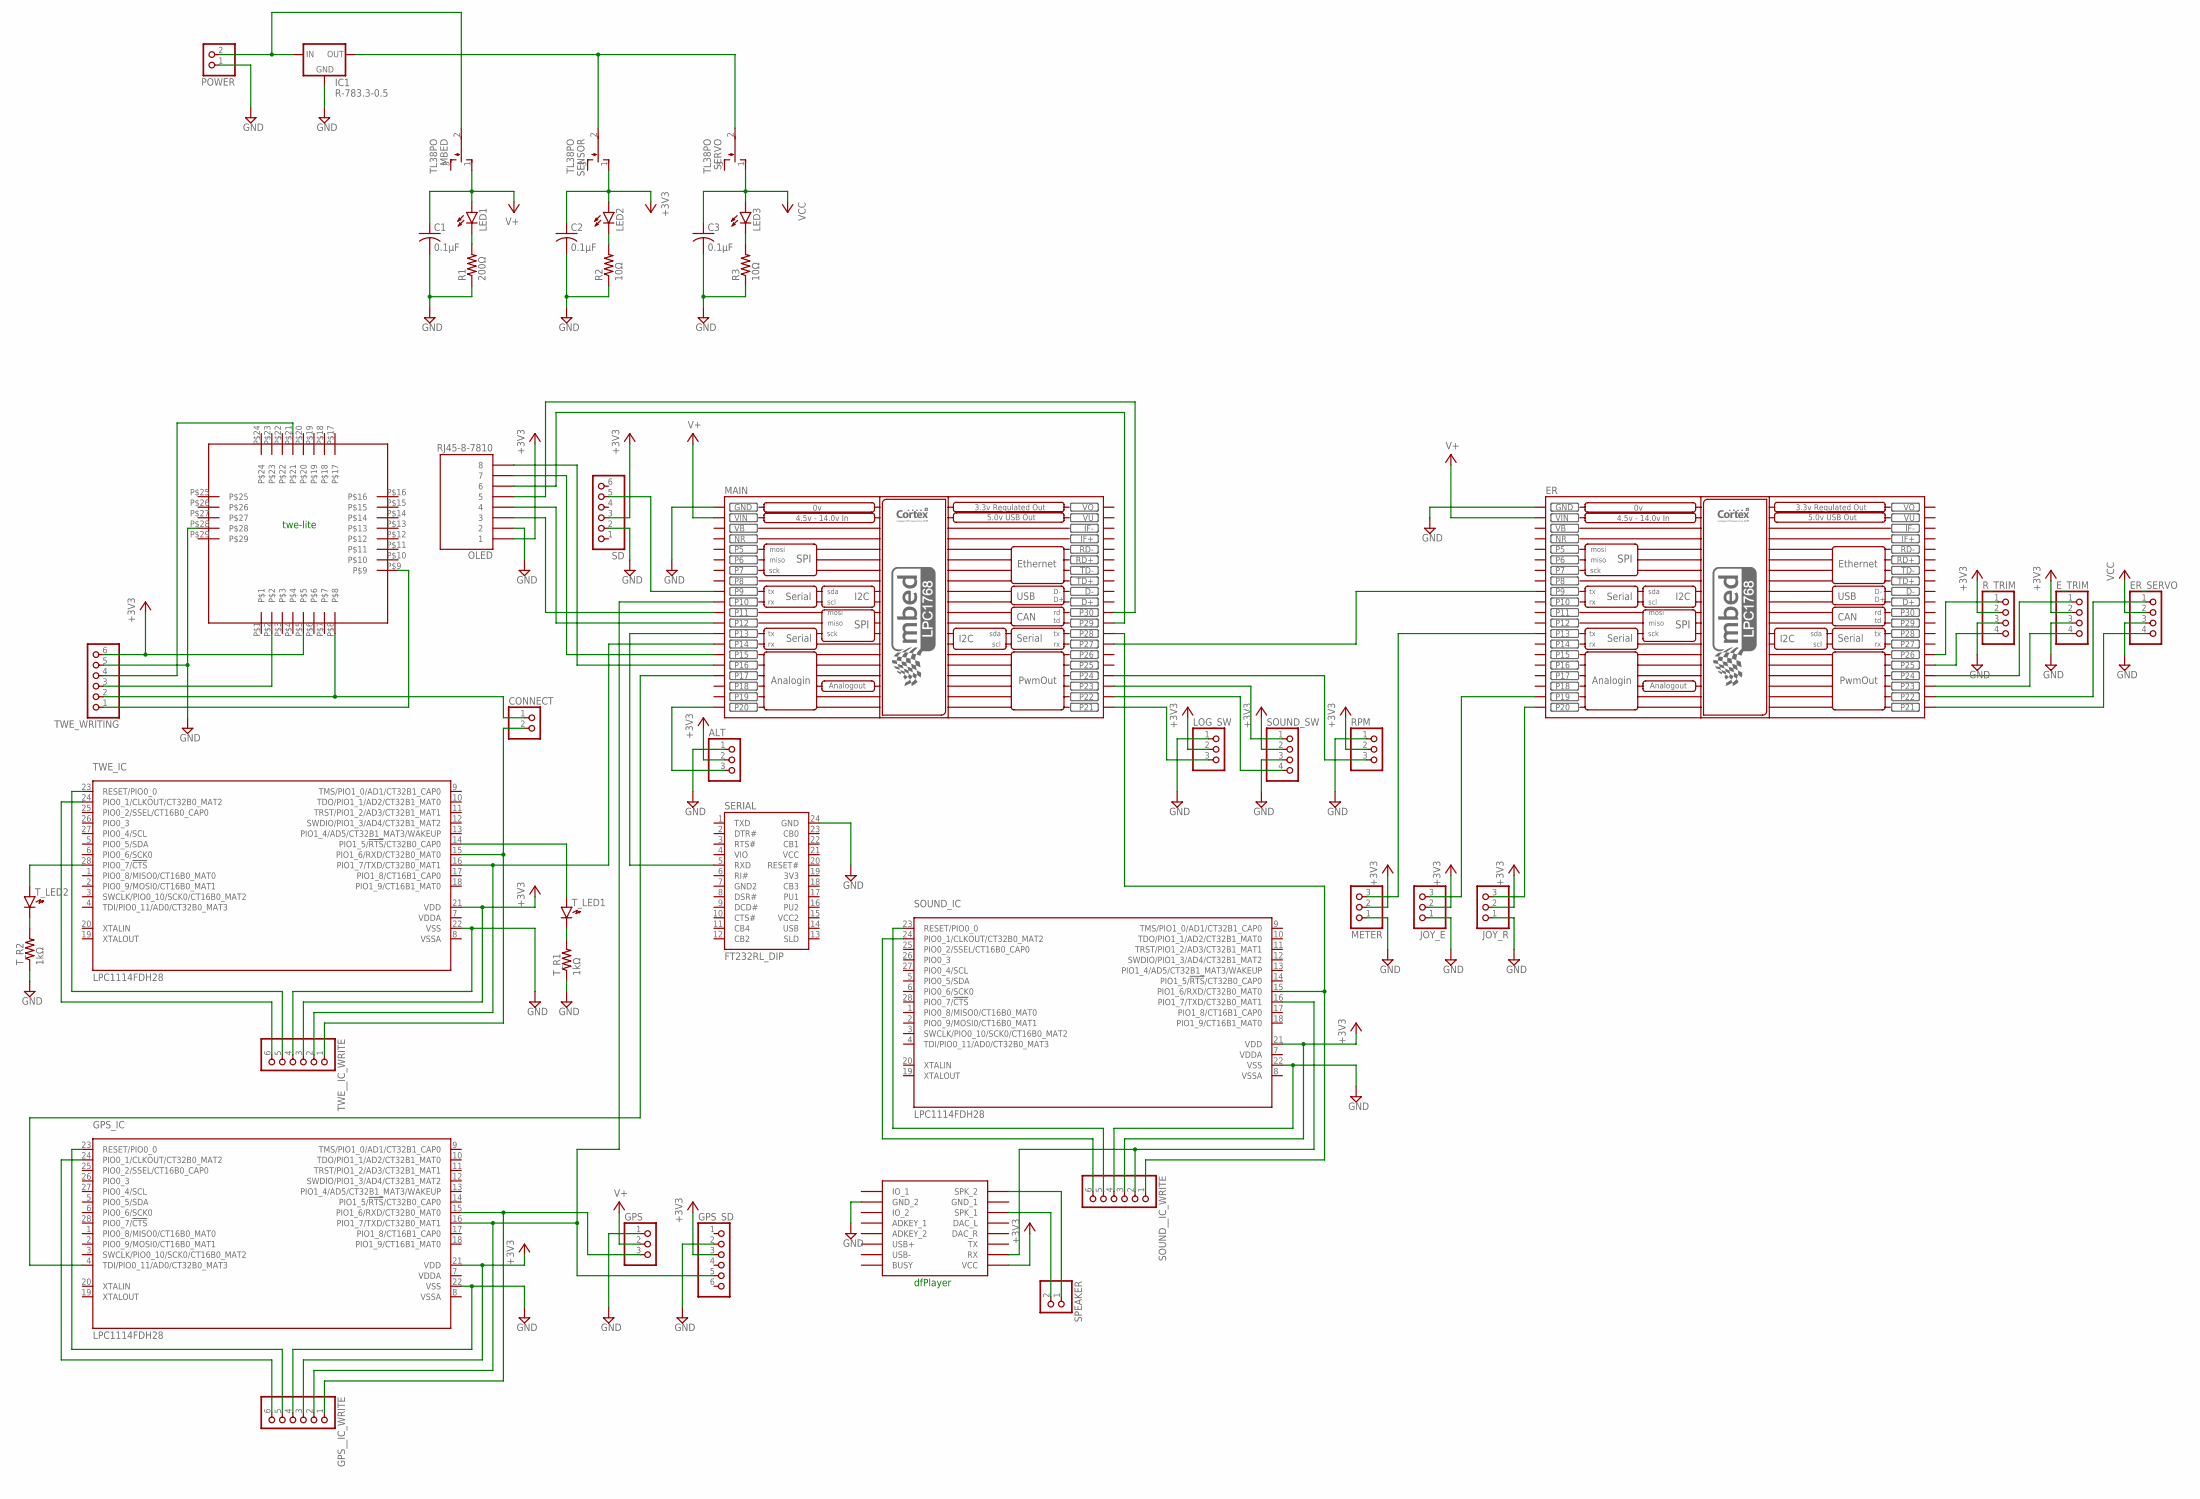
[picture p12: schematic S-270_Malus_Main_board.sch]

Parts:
ALT: PINHD-1X3; 1X03
C1, C2, C3: 0.1μF; C0603
CONNECT: PINHD-1X2; 1X02
ER: MBED_NXP_LPC1768; MBED-KIT
ER_SERVO: PINHD-1X4/90; 1X04/90
E_TRIM: PINHD-1X4; 1X04
GPS: PINHD-1X3; 1X03
GPS_IC: LPC1114FDH28; SOT361-1
GPS_SD: PINHD-1X6; 1X06
GPS__IC_WRITE: PINHD-1X6; 1X06
IC1: R-783.3-0.5; SIP3
JOY_E: PINHD-1X3; 1X03
JOY_R: PINHD-1X3; 1X03
LED1, LED2, LED3: LED3MM
LOG_SW: PINHD-1X3; 1X03
MAIN: MBED_NXP_LPC1768; MBED-KIT
MBED: TL38PO; TL3XPO
METER: PINHD-1X3; 1X03
OLED: RJ45-8-7810; RJ-45_7810-8P8C
POWER: PINHD-1X2; 1X02
R1: 200Ω; R0603
R2, R3: 10Ω; R0603
RPM: PINHD-1X3; 1X03
R_TRIM: PINHD-1X4; 1X04
SD: PINHD-1X6; 1X06
SENSOR: TL38PO; TL3XPO
SERIAL: FT232RL_DIP
SERVO: TL38PO; TL3XPO
SOUND_IC: LPC1114FDH28; SOT361-1
SOUND_SW: PINHD-1X4; 1X04
SOUND__IC_WRITE: PINHD-1X6; 1X06
SPEAKER: PINHD-1X2; 1X02
TWE_IC: LPC1114FDH28; SOT361-1
TWE_WRITING: PINHD-1X6; 1X06
TWE__IC_WRITE: PINHD-1X6; 1X06
T_LED1, T_LED2: LED1608
T_R1, T_R2: 1kΩ; R0603
U$1: DFPLAYER
U$2: LITE

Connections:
+3V3: ALT.2, C2.1, E_TRIM.2, GPS_IC.21 (VDD), GPS_SD.3, GPS__IC_WRITE.3, JOY_E.2, JOY_R.2, LED2.A, LOG_SW.2, METER.2, OLED.1, RPM.2, R_TRIM.2, SD.3, SENSOR.1 (O), SOUND_IC.21 (VDD), SOUND_SW.2, SOUND__IC_WRITE.3, TWE_IC.21 (VDD), TWE_WRITING.6, TWE__IC_WRITE.3, U$1.VCC, U$2.P$5
GND: ALT.1, C1.2, C2.2, C3.2, ER.GND, ER_SERVO.3, E_TRIM.3, GPS.1, GPS_IC.22 (VSS), GPS_SD.2, GPS__IC_WRITE.4, IC1.2 (GND), JOY_E.1, JOY_R.1, LOG_SW.1, MAIN.GND, METER.1, OLED.2, POWER.1, R1.1, R2.1, R3.1, RPM.1, R_TRIM.3, SD.2, SERIAL.24 (GND), SOUND_IC.22 (VSS), SOUND_SW.3, SOUND__IC_WRITE.4, TWE_IC.22 (VSS), TWE_WRITING.5, TWE__IC_WRITE.4, T_R1.1, T_R2.1, U$1.GND_2, U$2.P$28
unnamed: IC1.1 (IN), MBED.2, POWER.2
unnamed: LED1.K (C), R1.2
unnamed: LOG_SW.3, MAIN.P$21 (P21)
unnamed: LED3.K (C), R3.2
unnamed: LED2.K (C), R2.2
unnamed: MAIN.P$24 (P24), RPM.3
unnamed: MAIN.P$9 (P9), SD.5
unnamed: IC1.3 (OUT), SENSOR.2, SERVO.2
unnamed: MAIN.P$23 (P23), SOUND_SW.1
unnamed: MAIN.P$11 (P11), OLED.3
unnamed: MAIN.P$22 (P22), SOUND_SW.4
unnamed: MAIN.P$12 (P12), OLED.4
unnamed: MAIN.P$30 (P30), OLED.5
unnamed: MAIN.P$29 (P29), OLED.6
unnamed: MAIN.P$15 (P15), OLED.7
unnamed: MAIN.P$16 (P16), OLED.8
unnamed: GPS_IC.23 (RESET/PIO0_0), GPS__IC_WRITE.5
unnamed: GPS_IC.24 (PIO0_1/CLKOUT/CT32B0_MAT2), GPS__IC_WRITE.6
unnamed: GPS_IC.16 (PIO1_7/TXD/CT32B0_MAT1), GPS_SD.5, GPS__IC_WRITE.2, MAIN.P$10 (P10)
unnamed: GPS.3, GPS_IC.15 (PIO1_6/RXD/CT32B0_MAT0), GPS__IC_WRITE.1
unnamed: SOUND_IC.23 (RESET/PIO0_0), SOUND__IC_WRITE.5
unnamed: SOUND_IC.24 (PIO0_1/CLKOUT/CT32B0_MAT2), SOUND__IC_WRITE.6
unnamed: TWE_IC.23 (RESET/PIO0_0), TWE__IC_WRITE.5
unnamed: TWE_IC.24 (PIO0_1/CLKOUT/CT32B0_MAT2), TWE__IC_WRITE.6
unnamed: SOUND_IC.16 (PIO1_7/TXD/CT32B0_MAT1), SOUND__IC_WRITE.2, U$1.RX
unnamed: MAIN.P$28 (P28), SOUND_IC.15 (PIO1_6/RXD/CT32B0_MAT0), SOUND__IC_WRITE.1
unnamed: MAIN.P$14 (P14), TWE_IC.16 (PIO1_7/TXD/CT32B0_MAT1), TWE__IC_WRITE.2
unnamed: CONNECT.2, TWE_IC.15 (PIO1_6/RXD/CT32B0_MAT0), TWE__IC_WRITE.1
unnamed: TWE_IC.14 (PIO1_5/!RTS!/CT32B0_CAP0), T_LED1.A
unnamed: SPEAKER.2, U$1.SPK1 (SPK_1)
unnamed: SPEAKER.1, U$1.SPK2 (SPK_2)
unnamed: T_LED1.K, T_R1.2
unnamed: TWE_IC.28 (PIO0_7/!CTS!), T_LED2.A
unnamed: T_LED2.K, T_R2.2
unnamed: MAIN.P$13 (P13), SERIAL.5 (RXD)
unnamed: ALT.3, MAIN.P$20 (P20)
unnamed: TWE_WRITING.4, U$2.P$21
unnamed: TWE_WRITING.3, U$2.P$2
unnamed: CONNECT.1, TWE_WRITING.2, U$2.P$8
unnamed: TWE_WRITING.1, U$2.P$9
unnamed: GPS_IC.4 (TDI/PIO0_11/AD0/CT32B0_MAT3), MAIN.P$17 (P17)
unnamed: ER.P$9 (P9), MAIN.P$27 (P27)
unnamed: ER.P$13 (P13), METER.3
unnamed: ER.P$19 (P19), JOY_E.3
unnamed: ER.P$20 (P20), JOY_R.3
unnamed: ER.P$26 (P26), R_TRIM.1
unnamed: ER.P$24 (P24), E_TRIM.1
unnamed: ER.P$25 (P25), R_TRIM.4
unnamed: ER.P$23 (P23), E_TRIM.4
unnamed: ER.P$22 (P22), ER_SERVO.1
unnamed: ER.P$21 (P21), ER_SERVO.4
NR: ER.NR, MAIN.NR
V+: C1.1, ER.VIN, GPS.2, LED1.A, MAIN.VIN, MBED.1 (O)
VB: ER.VB, MAIN.VB
VCC: C3.1, ER_SERVO.2, LED3.A, SERVO.1 (O)
VDDA: GPS_IC.7 (VDDA), SOUND_IC.7 (VDDA), TWE_IC.7 (VDDA)
VO: ER.VOUT (VO), MAIN.VOUT (VO)
VSSA: GPS_IC.8 (VSSA), SOUND_IC.8 (VSSA), TWE_IC.8 (VSSA)
VU: ER.VU, MAIN.VU

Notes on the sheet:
twe-lite
dfPlayer

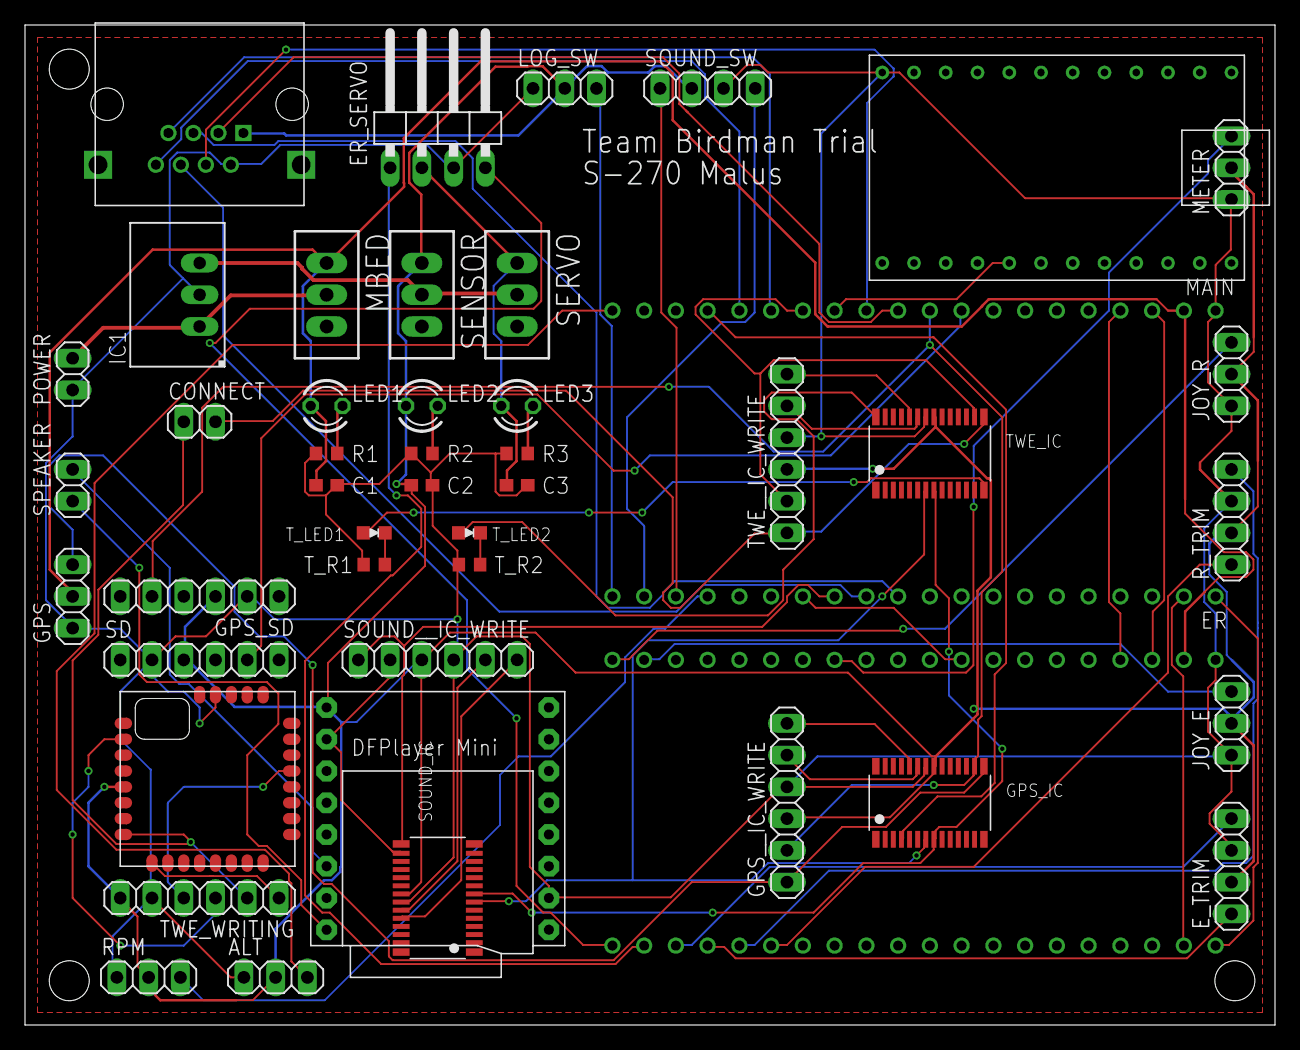
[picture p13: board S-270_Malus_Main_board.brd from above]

Board: 2 copper layers, 100.0 x 80.0 mm, 46 parts (0 on the bottom side), 61 nets.

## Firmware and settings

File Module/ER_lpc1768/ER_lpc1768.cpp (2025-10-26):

#include"mbed.h"

//Neutral Pulse幅 0.00151 ± 0.0006 s
//サーボモータのトルクによりニュートラル位置がズレていく可能性あり

//-----------------S-270 Malus 操舵システム-------------------
//サーボ角度: -10° ~ +10°
//エレベータ: 10段階
//ラダー: 3段階

//Duty Cicle 100% ?

/*-----------------PC モード用 パルス幅-----------------*/
#define UP_STAGE4    0.000030  //オーバーフロー ? 回転し続けてしまう
#define UP_STAGE3    0.000400  //オーバーフロー ? 回転し続けてしまう
#define UP_STAGE2    0.000770  
#define UP_STAGE1    0.001140
#define NEUTRAL_E    0.001510
#define DOWN_STAGE1  0.001880
#define DOWN_STAGE2  0.002250
#define DOWN_STAGE3  0.002620  //オーバーフロー ? 回転し続けてしまう
#define DOWN_STAGE4  0.002990  //オーバーフロー ? 回転し続けてしまう

#define LEFT_STAGE4  0.000030  //オーバーフロー ? 回転し続けてしまう
#define LEFT_STAGE3  0.000400  //オーバーフロー ? 回転し続けてしまう
#define LEFT_STAGE2  0.000770
#define LEFT_STAGE1  0.001140
#define NEUTARL_R    0.001510
#define RIGHT_STAGE1 0.001880
#define RIGHT_STAGE2 0.002250
#define RIGHT_STAGE3 0.002620  //オーバーフロー ? 回転し続けてしまう
#define RIGHT_STAGE4 0.002990  //オーバーフロー ? 回転し続けてしまう

Serial pc(USBTX,USBRX);

PwmOut pwm_ele(p22);
PwmOut pwm_rud(p21);

char start_command;
char pc_command;
char pc_ele_command;
char pc_rud_command;

void pc_control();
void control();

int main()
{
    pc.attach(pc_control,Serial::RxIrq);

    while(1){

    }
}

void pc_control()
{
    start_command = pc.getc();

    if(start_command == '\r'){ //TeraTerm 上でEnterが押されたら, PC mode 突入

        while(1){

            pc.printf("Start PC mode \r\n");
                
            pc.printf("=================================================== \r\n");
            pc.printf("Push the PC key \r\n");
            pc.printf("\r\n");
            pc.printf("Elevator Control : E \r\n");
            pc.printf("Rudder Control : R \r\n");
            pc.printf("Finish PC mode : C \r\n");
            pc.printf("\r\n");

            while(1){

                pc_command = pc.getc();//入力キーのデータ格納

                if(pc_command == 'E'){

                    pc.printf(" 'Elevator Control' selected \r\n");
                    pc.printf("\r\n");

                    pc.printf("Please set pulse width (Elevator) \r\n");
                    pc.printf("\r\n");

                    pc.printf("UP_stage4 : 1 \r\n");
                    pc.printf("UP_stage3 : 2 \r\n");
                    pc.printf("UP_stage2 : 3 \r\n");
                    pc.printf("UP_stage1 : 4 \r\n");

                    pc.printf("Neutral_E : 5 \r\n");

                    pc.printf("DOWN_stage1 : 6 \r\n");
                    pc.printf("DOWN_stage2 : 7 \r\n");
                    pc.printf("DOWN_stage3 : 8 \r\n");
                    pc.printf("DOWN_stage4 : 9 \r\n");

                    pc.printf("Back : 0 \r\n");
                    pc.printf("\r\n");


                    while(1){

                        pc_ele_command = pc.getc();

                        /*---------エレベーター　パルス幅条件分岐---------*/

                        if(pc_ele_command == '1'){

                            pc.printf(" 'UP_stage4' selected\r\n");
                            pc.printf("\r\n");

                            pwm_ele.pulsewidth(UP_STAGE4);

                        } else if(pc_ele_command == '2'){

                            pc.printf(" 'UP_stage3' selected\r\n");
                            pc.printf("\r\n");

                            pwm_ele.pulsewidth(UP_STAGE3);

                        } else if(pc_ele_command == '3'){

                            pc.printf(" 'UP_stage2' selected\r\n");
                            pc.printf("\r\n");

                            pwm_ele.pulsewidth(UP_STAGE2);

                        } else if(pc_ele_command == '4'){

                            pc.printf(" 'UP_stage1' selected\r\n");
                            pc.printf("\r\n");

                            pwm_ele.pulsewidth(UP_STAGE1);

                        } else if(pc_ele_command == '5'){

                            pc.printf(" 'Neutral_E' selected\r\n");
                            pc.printf("\r\n");

                            pwm_ele.pulsewidth(NEUTRAL_E);

                        } else if(pc_ele_command == '6'){

                            pc.printf(" 'Down_stage1' selected\r\n");
                            pc.printf("\r\n");

                            pwm_ele.pulsewidth(DOWN_STAGE1);

                        } else if(pc_ele_command == '7'){

                            pc.printf(" 'Down_stage2' selected\r\n");
                            pc.printf("\r\n");

                            pwm_ele.pulsewidth(DOWN_STAGE2);

                        } else if(pc_ele_command == '8'){

                            pc.printf(" 'Down_stage3' selected\r\n");
                            pc.printf("\r\n");

                            pwm_ele.pulsewidth(DOWN_STAGE3);

                        } else if(pc_ele_command == '9'){

                            pc.printf(" 'Down_stage4' selected\r\n");
                            pc.printf("\r\n");

                            pwm_ele.pulsewidth(DOWN_STAGE4);

                        } else if(pc_ele_command == '0'){

                            pc.printf(" finish 'Elevator Control mode' \r\n");
                            pc.printf("\r\n");

                            break;
                        }
                    }

                    break;

                } else if(pc_command == 'R'){

                    pc.printf(" 'Rudder Control' selected \r\n");

                    while(1){

                        pc.printf("Please set pulse width (Rudder) \r\n");
                        pc.printf("\r\n");

                        pc.printf("LEFT_stage4 : 1 \r\n");
                        pc.printf("LEFT_stage3 : 2 \r\n");
                        pc.printf("LEFT_stage2 : 3 \r\n");
                        pc.printf("LEFT_stage1 : 4 \r\n");

                        pc.printf("Neutral_R : 5 \r\n");

                        pc.printf("RIGHT_stage1 : 6 \r\n");
                        pc.printf("RIGHT_stage2 : 7 \r\n");
                        pc.printf("RIGHT_stage3 : 8 \r\n");
                        pc.printf("RIGHT_stage4 : 9 \r\n");

                        pc.printf("Back : 0 \r\n");
                        pc.printf("\r\n");

                        while(1){

                            pc_rud_command = pc.getc();

                            /*-----------ラダー　パルス幅条件分岐-----------*/

                            if(pc_rud_command == '1'){

                                pc.printf(" 'LEFT_stage4' selected\r\n");
                                pc.printf("\r\n");

                                pwm_rud.pulsewidth(LEFT_STAGE4);

                            } else if(pc_rud_command == '2'){

                                pc.printf(" 'LEFT_stage3' selected\r\n");
                                pc.printf("\r\n");

                                pwm_rud.pulsewidth(LEFT_STAGE3);

                            } else if(pc_rud_command == '3'){

                                pc.printf(" 'LEFT_stage2' selected\r\n");
                                pc.printf("\r\n");

                                pwm_rud.pulsewidth(LEFT_STAGE2);

                            } else if(pc_rud_command == '4'){

                                pc.printf(" 'LEFT_stage1' selected\r\n");
                                pc.printf("\r\n");

                                pwm_rud.pulsewidth(LEFT_STAGE1);

                            } else if(pc_rud_command == '5'){

                                pc.printf(" 'Neutral_R' selected \r\n");
                                pc.printf("\r\n");

                                pwm_rud.pulsewidth(NEUTARL_R);

                            } else if(pc_rud_command == '6'){

                                pc.printf(" 'RIGHT_stage1' selected\r\n");
                                pc.printf("\r\n");

                                pwm_rud.pulsewidth(RIGHT_STAGE1);

                            } else if(pc_rud_command == '7'){

                                pc.printf(" 'RIGHT_stage2' selected\r\n");
                                pc.printf("\r\n");

                                pwm_rud.pulsewidth(RIGHT_STAGE2);

                            } else if(pc_rud_command == '8'){

                                pc.printf(" 'RIGHT_stage3' selected\r\n");
                                pc.printf("\r\n");

                                pwm_rud.pulsewidth(RIGHT_STAGE3);

                            } else if(pc_rud_command == '9'){

                                pc.printf(" 'RIGHT_stage4' selected\r\n");
                                pc.printf("\r\n");

                                pwm_rud.pulsewidth(RIGHT_STAGE4);

                            } else if(pc_rud_command == '0'){
                                pc.printf(" finish 'Rudder Control mode' \r\n");
                                pc.printf("\r\n");

                                break;
                            }
                        }

                        break;
                    }

                } else if(pc_command == 'C'){

                    pc.printf("finish 'PC mode' \r\n");
                    pc.printf("\r\n");

                    break;

                }

            } 
        }
    }
}

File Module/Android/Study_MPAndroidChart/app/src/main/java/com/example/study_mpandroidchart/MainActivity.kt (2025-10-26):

package com.example.study_mpandroidchart

import android.Manifest
import android.content.Context
import android.content.Intent
import android.content.pm.PackageManager
import android.hardware.usb.UsbDeviceConnection
import android.hardware.usb.UsbManager
import android.location.Location
import android.location.LocationListener
import android.location.LocationManager
import androidx.appcompat.app.AppCompatActivity
import android.os.Bundle
import android.provider.Settings
import android.util.Log
import android.view.View
import android.view.WindowManager
import android.widget.Toast
import androidx.core.app.ActivityCompat
import androidx.core.content.ContextCompat
import com.hoho.android.usbserial.driver.UsbSerialDriver
import com.hoho.android.usbserial.driver.UsbSerialPort
import com.hoho.android.usbserial.driver.UsbSerialProber
import com.hoho.android.usbserial.util.SerialInputOutputManager
import java.lang.Exception
import kotlin.concurrent.thread

open class MainActivity : AppCompatActivity(), LocationListener {

    private val spdKey = "SPD"
    private val mapKey = "MAP"
    private val altKey = "ALT"
    private val timerKey = "TIME"
    private lateinit var locationManager: LocationManager
    override fun onCreate(savedInstanceState: Bundle?) {
        super.onCreate(savedInstanceState)
        setContentView(R.layout.activity_main)
        window.addFlags(WindowManager.LayoutParams.FLAG_KEEP_SCREEN_ON)
        val fragmentManager = supportFragmentManager
        val fragmentTransaction = fragmentManager.beginTransaction()//トランザクション開始
        fragmentTransaction.add(R.id.alt_container, Altitude())
        fragmentTransaction.commit()//トランザクション終了

        val manager: UsbManager = getSystemService(Context.USB_SERVICE) as UsbManager
        val availableDrivers: List<UsbSerialDriver> =
            UsbSerialProber.getDefaultProber().findAllDrivers(manager)

        if (availableDrivers.isEmpty()) {
            Toast.makeText(this, "USBCom:ドライバ該当なし", Toast.LENGTH_LONG).show()
        } else {
            val driver: UsbSerialDriver = availableDrivers[0]
            val connection: UsbDeviceConnection = manager.openDevice(driver.device)
            if (connection == null) { //Condition 'connection == null' is always 'false'って真か？
                //manager.requestPermission(driver.device,) 権限求める操作入れると親切なアプリになります。
                Toast.makeText(this, "USBCom:権限がありません", Toast.LENGTH_LONG).show()
            } else {
                port = driver.ports[0]
                port.open(connection)
                port.setParameters(112500, 8, UsbSerialPort.STOPBITS_1, UsbSerialPort.PARITY_NONE)
                Toast.makeText(this, "USBCom:接続されました", Toast.LENGTH_LONG).show()
                var usbIoManager = SerialInputOutputManager(port, Listener())
                thread {
                    usbIoManager.start()
                }
            }
        }
    }


    private fun locationStart() {
        Log.d("debug", "locationStart()")

        // Instances of LocationManager class must be obtained using Context.getSystemService(Class)
        locationManager = getSystemService(Context.LOCATION_SERVICE) as LocationManager

        val locationManager = getSystemService(Context.LOCATION_SERVICE) as LocationManager

        if (locationManager.isProviderEnabled(LocationManager.GPS_PROVIDER)) {
            Log.d("debug", "location manager Enabled")
        } else {
            // to prompt setting up GPS
            val settingsIntent = Intent(Settings.ACTION_LOCATION_SOURCE_SETTINGS)
            startActivity(settingsIntent)
            Log.d("debug", "not gpsEnable, startActivity")
        }

        if (ContextCompat.checkSelfPermission(this,
                Manifest.permission.ACCESS_FINE_LOCATION) != PackageManager.PERMISSION_GRANTED) {
            ActivityCompat.requestPermissions(this,
                arrayOf(Manifest.permission.ACCESS_FINE_LOCATION), 1000)

            Log.d("debug", "checkSelfPermission false")
            return
        }

    }

    //フルスクリーン↓ by公式リファレンス
    override fun onWindowFocusChanged(hasFocus: Boolean) {
        super.onWindowFocusChanged(hasFocus)
        if (hasFocus) hideSystemUI()
    }

    private fun hideSystemUI() {
        // Enables regular immersive mode.
        // For "lean back" mode, remove SYSTEM_UI_FLAG_IMMERSIVE.
        // Or for "sticky immersive," replace it with SYSTEM_UI_FLAG_IMMERSIVE_STICKY
        window.decorView.systemUiVisibility = (View.SYSTEM_UI_FLAG_IMMERSIVE
                // Set the content to appear under the system bars so that the
                // content doesn't resize when the system bars hide and show.
                or View.SYSTEM_UI_FLAG_LAYOUT_STABLE
                or View.SYSTEM_UI_FLAG_LAYOUT_HIDE_NAVIGATION
                or View.SYSTEM_UI_FLAG_LAYOUT_FULLSCREEN
                // Hide the nav bar and status bar
                or View.SYSTEM_UI_FLAG_HIDE_NAVIGATION
                or View.SYSTEM_UI_FLAG_FULLSCREEN)
    }

    //フルスクリーン↑

    lateinit var port: UsbSerialPort
    private var newLat:Double=0.0
    private var newLon:Double=0.0

    override fun onLocationChanged(location: Location) {
        newLat = location.latitude
        newLon = location.longitude
    }

    private inner class Listener : SerialInputOutputManager.Listener {
        override fun onRunError(e: Exception?) {
            return
        }

        override fun onNewData(data: ByteArray) {
            check(data, data.size)

        }
    }

    private val corrctData = mutableListOf<Byte>()
    private fun check(data: ByteArray, length: Int) { // 確認処理
        if (length == 12) {//繋がってきたとき
            detection(data)
            corrctData.clear()//リセット。（不正データの後に正しいデータが入るとfix関数のclear()が実行されないため。
        } else if (length < 12) {//分離されてきたとき
            correction(length, data)
        }
    }

    private fun correction(length: Int, data: ByteArray) { //データ補正
        for (i in 0 until length) {
            corrctData += data[i]
        }
        if (corrctData.size == 12) {
            detection(corrctData.toByteArray())//mutableList<Byte>で宣言されているため、ByteArrayに統一
            corrctData.clear()
        }
    }


    private fun detection(data: ByteArray) {//誤り検知
        var spdValue: Float
        var altValue: Float
        var txCkSum: Int
        var rxCkSum: Int
        if (data[0].toChar() == 'S') {
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

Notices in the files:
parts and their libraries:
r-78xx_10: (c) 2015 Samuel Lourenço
